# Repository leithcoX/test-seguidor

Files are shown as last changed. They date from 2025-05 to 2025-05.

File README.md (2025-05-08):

# Robot Seguidor de Línea

Test de seguidor de línea para competiciones.
Nombre pendiente.

## Estructura del proyecto
Boceto de la estructura del proyecto

```bash
.
├── placa_sensor
│   ├── kicad_sch
│   └── kicad_pcb
├── placa_seguidor
│   ├── kicad_sch
│   └── kicad_pcb
├── modelo
│   └── seguidor.FCStd
├── include
│   ├── file1.h
│   └── file2.h
├── src
│   ├── file1.ino
│   └── file2.ino
├── res
│   ├── datasheets.pdf
│   ├── images.png
│   └── referencias o links
└── README.md
```

## Requisitos
 - 20cm largo x 14cm de ancho x 10cm de alto
 - Area mínima de 23mm x 14mm. Visible. No pueden ser secciones de la batería.
 - No control remoto, o que solo de la orden de salida
 - Indicador luminoso (fijo o intermitente) que muestra cuando el robot inicia a correr.
 - Ruedas sin adherentes

## TODOs
 - ~~Rediseñar la placa de sensores (corregir errores) y mandar al lci~~
 - ~~Puente H~~
 - ~~Arduino Nano o ATmega328~~ y programarlo
 - ~~Comprar Placa Experimental~~
 - Elegir batería
 - Hacer un diagrama tal vez de como seguir el proyecto
 - ~~Hacér una bitácora~~ (subirla al repo?)
 - Agregar vista general del proyecto desde la página principal
 - ~~Agregar una lista de compras que puedan editar todos~~
 - Terminar de Soldar/limpiar modulo de sensores chequeando continuidad (Ciin lo hace el jueves)
 - Probar modulo se sensores con arduino (Armar código de prueba) 
 - 

## Artículos pendientes
 - 2 Capacitores 100nf (Puente H)
 - 10 x Diodos 1N4007  (Puente H)
 - 1 x Zócalo ZT16A (Zocalo 16 pines para puente H)

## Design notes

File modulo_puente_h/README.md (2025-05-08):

# Modulo Puente H

Este módulo se encarga de controlar los motores a partir de las entradas recibidas por sus pines.

Las pistas azules representan conexiones físicas cableadas por nosotros ya que el diseño no es posible en una placa simple faz.

![Front preview de la placa]() 


## TODOs
 - [ ] Revisar las medidas de la placa
 - [ ] Hacer los agujeros para las medidas del modelo 3D
 - [ ] El regulador de tensión debería ir en este módulo?
 - [ ] Revisar las conexiones
 - [ ] Replantearse el diseño del puente h, ¿Qué tensión tienen los motores?

#### Nota

Considerar que se podría diseñar todo en la parte posterior y soldar los componentes del lado que no tiene cobre.

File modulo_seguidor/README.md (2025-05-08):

# Modulo Seguidor

Este módulo se encarga de ejecutar las funciones propias de un seguidor de línea, procesar las lecturas del módulo sensor y dirigir los motores.

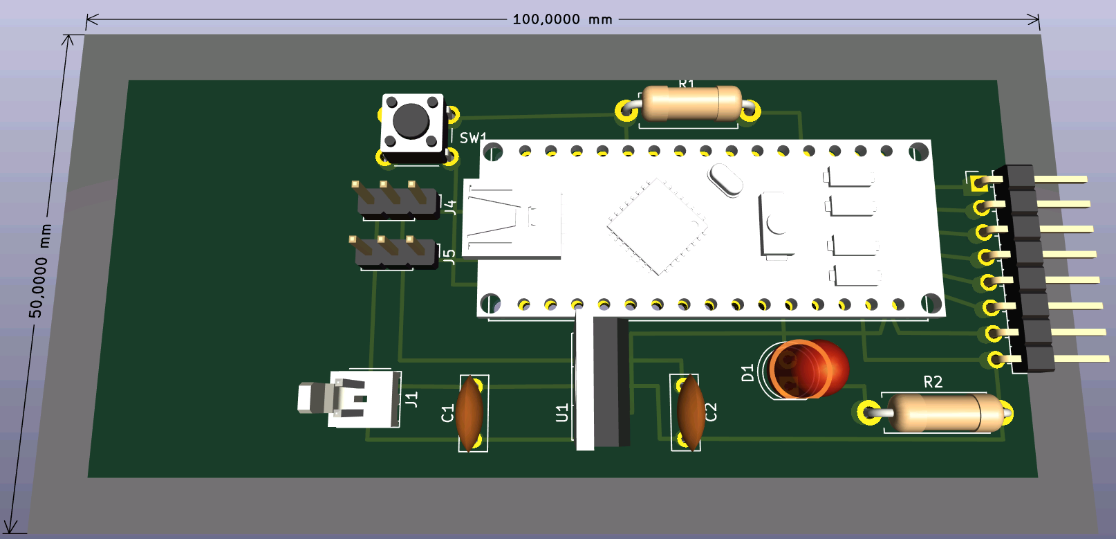
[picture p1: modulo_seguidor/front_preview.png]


Vista previa de la placa desde arriba

## Referencia

Para el diseño en kicad se realizó una configuración para editar la placa como si se editara una placa perforada.

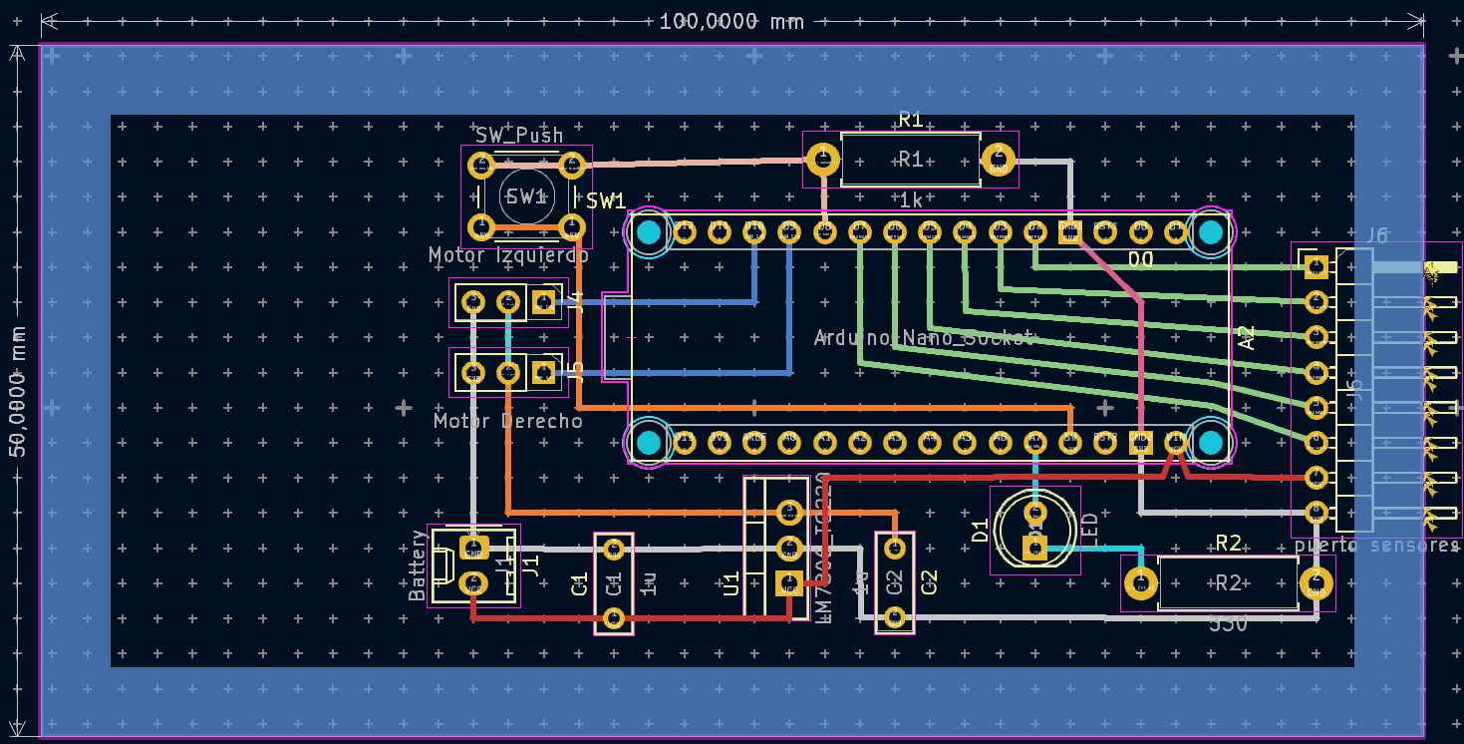
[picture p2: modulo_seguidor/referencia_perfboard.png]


Las marcas de cruces representan los agujeros de la placa perforada.
Las zonas sombreadas en los bordes tienen 5mm de ancho y representan la parte que no tiene agujeros en la placa perforada.
Si no se puede acomodar el componente se presiona CTRL mientras se arrastra para hacer un ajuste fino.

Más información al respecto en [foro de arduino](https://forum.arduino.cc/t/perfboard-circuit-design-with-kicad/1283999)

## TODOs
 - ~~Revisar las medidas de la placa (tomar en cuenta los bordes de la placa que no tienen agujeros)~~
 - Revisar los footprints de las resistencias y de los capacitores
 - ~~Acomodar los componentes y hacer las conexiones~~
 - Exportar a un modelo 3D (opcional)

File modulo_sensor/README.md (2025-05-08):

# Modulo de sensores

Este módulo se encarga de la lectura de la línea.

[comment]: Hacer_alguna_descripción_más

Vista previa de la PCB desde arriba



Vista previa de la PCB desde abajo



## TODOs
En orden de prioridad
- ~~Automatizar exportar los archivos de fabricación~~
- Hacer las pistas más grandes si es posible
- El script debe exportar a PDF ambos lados en la misma hoja conservando las dimensiones para imprimir el circuito.
- ~~Exportar a otros formatos (SVG, STEP, etc)~~
- Agregar alguna compatibilidad para Windows(?
- Agregar algun check para el momento de subir a Github
- Tal vez agregar algunas opciones para controlar el script(?
- Cambiar las rutas relativas con alguna variable de entorno(?

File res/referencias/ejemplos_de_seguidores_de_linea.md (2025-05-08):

## Links sobre distintos seguidores de linea 

https://youtu.be/CcIQNCyfTVk

https://tecnopatafisica.com/tecno3eso/teoria/robotica/105-arduino-robot-siguelineas

https://www.taloselectronics.com/blogs/tutoriales/robot-seguidor-de-linea-para-arduino-codigo

Referencia de internet


Un seguidor de línea del LABI
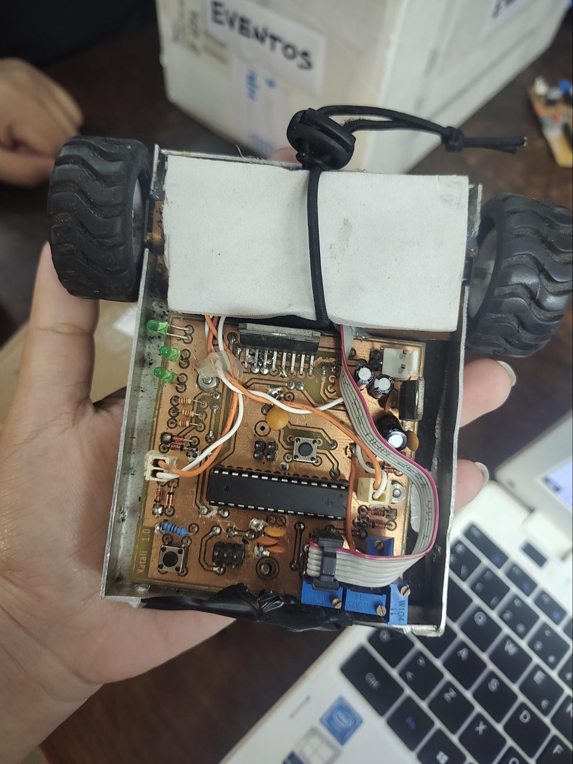
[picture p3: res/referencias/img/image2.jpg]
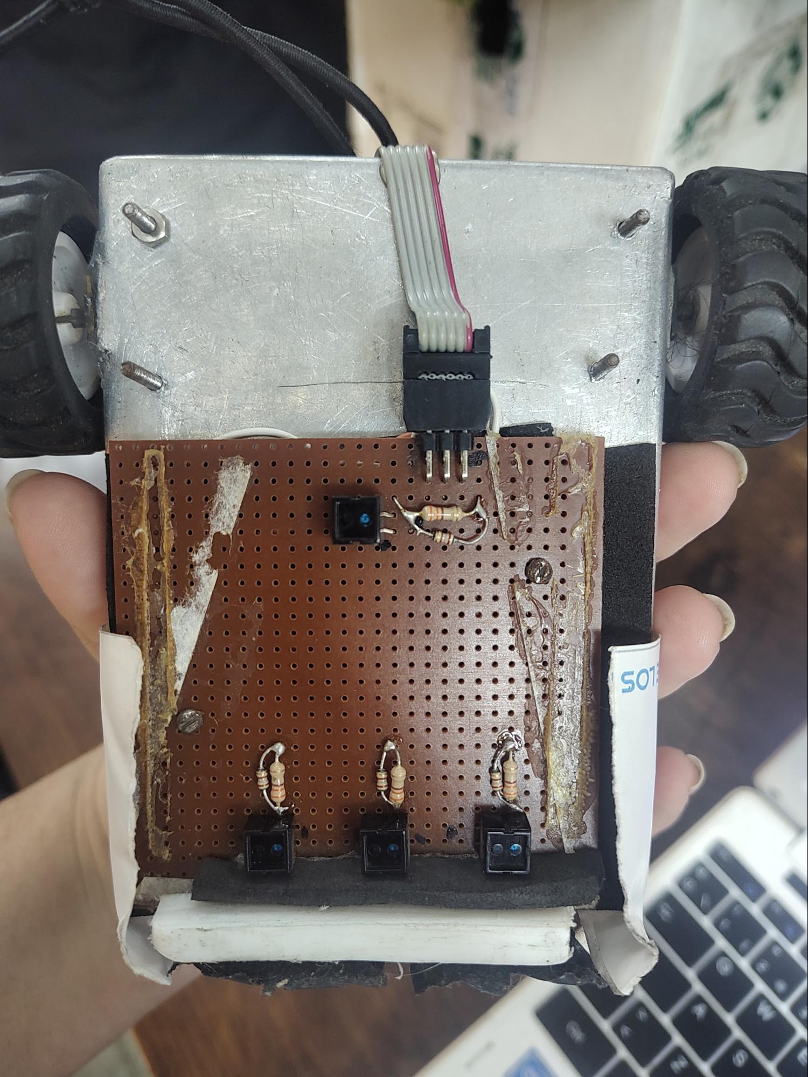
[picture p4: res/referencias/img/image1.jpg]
 

Otro más
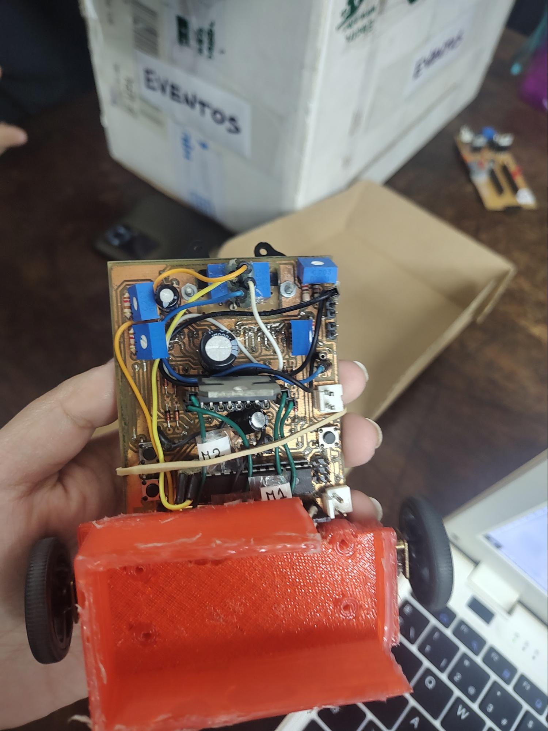
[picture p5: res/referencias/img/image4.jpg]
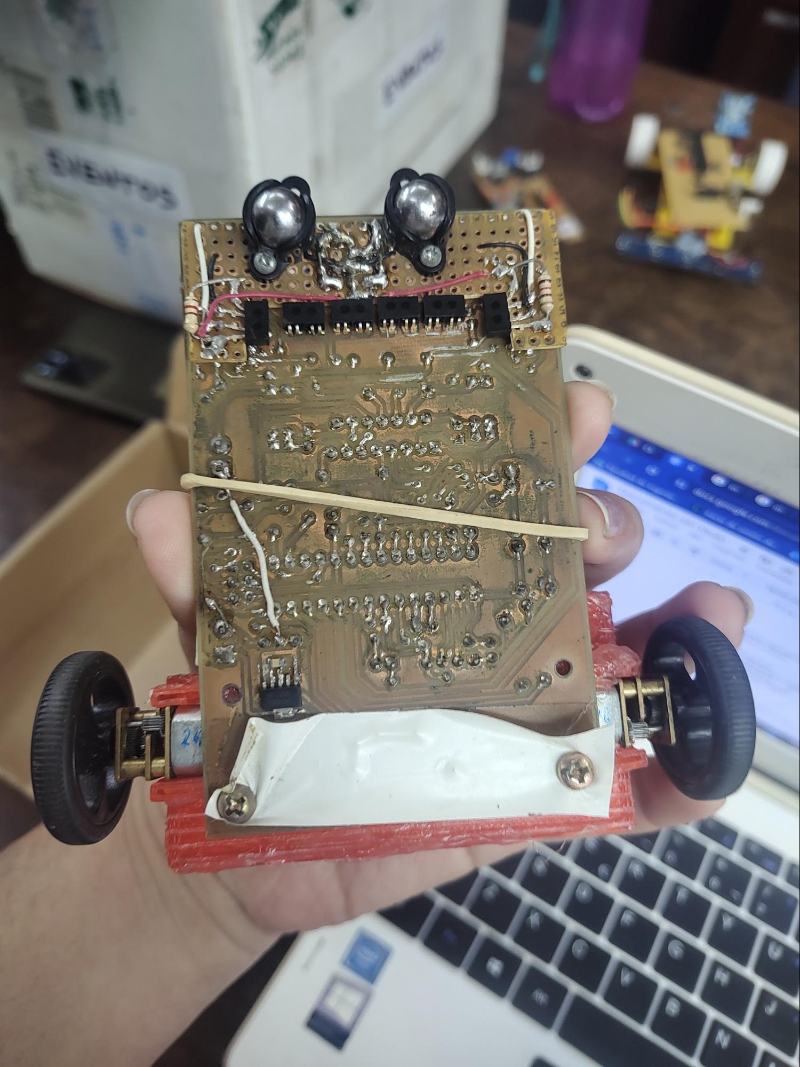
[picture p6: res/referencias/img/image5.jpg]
 

## Código

https://www.youtube.com/watch?v=w3bE3ygJMx8

## Puente H

Cómo usar un driver L298N

https://youtu.be/c0L4gNKwjRw?si=vZ1mv0ccFuuH0b-6

Esquemático de un driver genérico con L298N

https://newscrewdriver.com/2021/01/28/circuit-schematic-of-generic-l298n-driver-board/


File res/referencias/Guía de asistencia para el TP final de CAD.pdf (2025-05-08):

V2(2°Q 2020) | Guía de asistencia para el trabajo práctico final | ICAD 86.70

Autor: Zarauz Ignacio

## Guía de asistencia para el trabajo práctico final

Guía de asistencia para el trabajo práctico final

Introducción al diseño asistido por computadora (86.70) | 2

# Apartado técnico

Antes de continuar con la parte tangible del trabajo práctico asegúrese que su layout del PCB esté en condiciones. Verifique:

- Pistas: ancho indicado.
- Pads: tamaño apropiado (mínimo del área por defecto).
- Agujero de los pads: tamaño de sus brocas (recomendado, no esencial).

El ancho de sus pistas es de 20 mils (0,5 mm aproximadamente) ¿Qué importancia tiene esto? La importancia de esto será especificada más adelante.

La lista de precauciones para el PCB a continuación se debería detallar para explicar porque se deben aplicar, pero no se encuentra al alcance de las herramientas de física 2 (la cual, según el plan de estudios, se debe cursar en paralelo o antes de esta materia):

- Conectar el relleno de cobre a masa.
- Evitar pliegues de pistas en ángulos rectos.

El ancho de las pistas queda acotado por factores económicos, físicos y prácticos. Si hacemos pistas muy anchas estas ocuparán mayor superficie, el circuito aumentará de tamaño y necesitaremos placas muy grandes. Si fueran pistas fueran angostas existen al menos 3 problemas: el primero es que si decidimos hacer la placa con algún método poco profesional (como el del planchado) es probable que no queden fijadas las pistas sobre el cobre, en caso de que mejoremos el trazado de las pistas sobre el cobre todavía sigue siendo un riesgo el hecho de que el ácido puede comérselas. Si logramos resolver estos asuntos con técnicas profesionales aún queda un inconveniente físico que no podemos saltear.

# Realización del PCB

## ¿Qué ancho deben tener las pistas?

Seguro se habrá preguntado si existe algún motivo, además de la consigna, para elegir un ancho de 20 mils. A continuación, se trata de explicar con qué criterio puede escoger el ancho.

Si ya ha cursado física 2 sabrá que densidad de corriente es corriente sobre área. Básicamente, corriente es, un flujo de electrones en un área. Ahora ¿Cuál es nuestra área? Nuestra área es la sección de cobre de la pista, esta área depende de la altura del cobre (de la cual se hablará en la parte de ácido clorhídrico) que viene de fábrica y el ancho, el cual se lo da el ancho de la pista.

Al disminuir el ancho es totalmente análogo a quitar carriles de una autopista. Si sacamos carriles a la autopista el transito se empieza entorpecer y los autos deben circular con más cuidado para no chocarse unos con otros. Si seguimos sacando carriles llegará un momento en que no podrán circular más los autos. Algo similar ocurre con los electrones de la pista. Físicamente hablando, al disminuir el área la pista deja de funcionar como un conductor y empieza a ser una resistencia. Esto explica porque no podemos hacer tan fina la pista de cobre. En caso de haber corriente suficiente para hacer funcionar el dispositivo conectado a esa pista se podrían hacer trazados muy finos hasta el límite mínimo necesario para el dispositivo.

Para seguir manteniendo la corriente la tensión debe aumentar y esto provoca que la pista se caliente para disipar la energía. Como método alternativo a aumentar las pistas de ancho, en circuitos que ya tienen pistas muy anchas, algunos recurren a bañar la pista de cobre con estaño que, a pesar de no tener la misma conductividad que el cobre, es un buen conductor.

A continuación, y a lo largo de la parte técnica del documento, se encontrará con una selección de videos formativos útiles para la realización del trabajo. También se encontrarán videos optativos, de características informativas, que cumplen la función de complementar lo aprendido en la materia con usos que quedan fuera de los límites de la materia, pero que están vinculados a ella.

## Método de planchado

Este es, en caso de que no lo manden al LCI u otro servicio que se dedique a
realizar | PCB, | el | método | más
recomendado y barato. Parte del trabajo práctico es que pase por esta experiencia. Que sea barato no implica que sea de mala calidad, simplemente que las características del circuito, función y cantidad no son las indicadas para mandar a fabricar o realizar con el método de serigrafía.

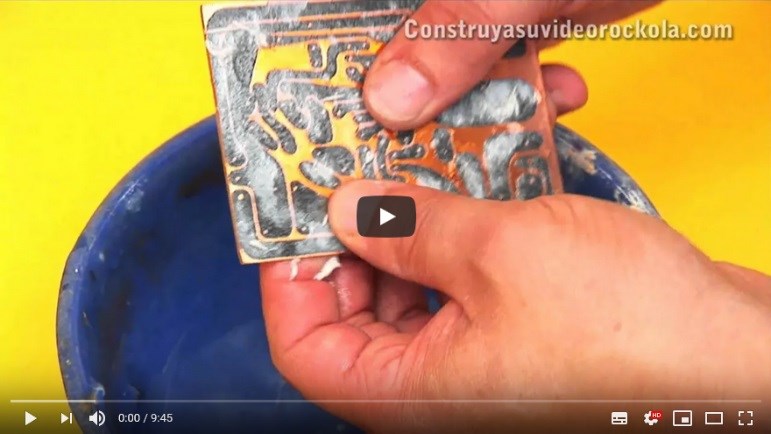
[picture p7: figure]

En cuanto a las técnicas las variantes que se pueden señalar es que en lugar de usar Thinner para remover el tóner se puede usar esponja de acero (virulana o la marca que sea), la misma que usa para limpiar el cobre antes de planchar. Es muy importante que la limpie. Asegúrese de usar la virulana que literalmente tiene densidad de esponja, visualmente esta está hecha de pequeñas fibras metálicas suaves que al usarla desprende fibras de la esponja. Se usa para limpiar metales blandos (bronce, cobre) ya que corren menos riesgo de ser rayados y le retiran los óxidos depositados.

Otro consejo, es que, al planchar, no solo limpie la placa, asegúrese que su impresión tenga el tamaño y espejado adecuado (cuando quede la tinta adherida al cobre debe verlo como quedará finalmente) y cuando vaya a colocar la hoja sobre el cobre preste mucha atención respecto a los bordes y la alineación. Si lo hace con cuidado, puede recortar primero la placa de cobre al tamaño de su circuito, o con un milímetro de margen si hay pistas pegadas al borde (recomendamos comprar una placa de 5x10 para tener al menos 2 intentos), para que el ácido tarde menos tiempo en retirar el cobre.

En cuanto a la alineación, al planchar, muchas veces no sale como uno espera. Recuerde hacerle unos márgenes, respecto a la impresión, al papel para que cumplan función de solapas que se plieguen al final de la placa la rodeen para pegarla con cinta. En caso de tener seguridad, y experiencia, podría poner una solapa y el resto mantenerlo con cinta a lo largo del borde. Esto no se recomienda mucho, ya que la cinta entorpece la conducción adecuada del calor hacia la tinta. Por la dificultad mencionada, se recomienda crear un PDF con múltiples cantidades de la impresión del PCB. Esto se puede hacer en una hoja usando programas como Inkscape, que es gratuito. Cuando lo haga asegúrese de que el dibujo conserve su tamaño original ¡lo mismo cuando ya este impreso! (las impresoras a veces están configuradas de manera tal que las dimensiones de la imagen se distorsionan). Puede aprovechar para crear una máscara de componentes casera (asegúrese de que el espejado sea el adecuado) imprimiendo la capa F.Fab (sobre la misma hoja) y planchándolo sobre la otra cara de la placa. Esto último suele salir mal, afortunadamente no es necesario para el trabajo. Requiere de más tiempo de planchado que la parte de cobre. También puede coordinar con compañeros para poner más de un modelo de PCB en la misma hoja.

Consejos para planchar. Si nunca ha tocado una es buen momento para aprender. No necesita experiencia previa. Claramente hágalo en seco (sin líquidos). Recuerde que es sobre la parte de cobre con algún papel entre la hoja de transferencia y la plancha. El tiempo de planchado depende de la potencia de la plancha y el papel de transferencia. Con una plancha por encima de los 80°C con 5 minutos en el lado del cobre alcanza (para el F.Fab puede necesitar 10). Puede dejar durante algún momento la plancha encima de este, pero durante al menos 2 minutos deslice con presión sobre el PCB, especialmente en los bordes y trozos de cinta, los bordes son muy importantes. Para darle unos retoques finales puede planchar directamente sobre el papel transfer. Una vez planchado sumergir inmediatamente en agua.

Una vez metido en el agua empezara a ver el resultado. Con las yemas de los dedos podrá retirar el papel. Algunos papeles dejan restos sobre los lugares que deberían ser comidos por el ácido. Para disminuir el tiempo en el ácido se recomienda repasar con un punzón aquellos lugares con el cobre expuesto. En caso de que alguna pista se haya cortado en el procedimiento este o el planchado se puede rescatar repasando, en el lugar que debería estar cubierto, con tinta con un marcador negro de tinta indeleble. Por experiencia, el Sharpie indeleble anda muy bien.

Algunos de los materiales, como la plancha, son comunes en los hogares, otros, como el ácido, posiblemente tenga que comprarlos. El Labi cuenta con plancha y herramientas para realizar este proceso. Lo único que tendría que aportar es un envase de plástico para poner el ácido y el ácido. El Labi le puede facilitar un papel de revista e imprimirlo en la fotocopiadora de la facultad. En caso de imprimirlo en su casa tenga en cuenta que la impresora debe ser laser y que las librerías y fotocopiadoras no dejan que les metan hojas texturas extrañas a sus fotocopiadoras o impresoras.

Antes de proseguir con otros videos esta bueno aclararle algunas cuestiones sobre el percloruro férrico, más allá de los cuidados que deba tomar (evitar contacto con la piel, ropa y superficies metálicas, opcional usar guantes, espacio ventilado y regular conscientemente la temperatura), para que pueda operar con un poco de conocimiento encima.

Cantidad y tiempo dependen de:

- Superficie placa.
- Superficie a comer.
- Temperatura del ácido.
- Movimiento del ácido.
- Concentración del ácido.

El percloruro férrico puede ser vendido como polvo o diluido (las proporciones varían). Lo más probable es que lo consiga en liquido (diluido), lo cual es parcialmente más seguro dado que evita aspirar partículas de polvo. A continuación, se hablará de las características que hay que contemplar acerca de este. El tiempo para una placa de estas dimensiones totalmente cubierta suele ser de más de 15 minutos.

Si la placa fuera más grande, seguro, sería más la cantidad de cobre a retirar. El mismo problema sucede si no está hecho el copper pour, ya que se retiran superficies de cobre que no influyen en este trabajo y el tiempo del proceso será mayor. Una alternativa al copper pour, que en este caso no se puede, es agrandar algunas pistas.

La eficiencia del ácido aumenta con temperaturas altas. En caso de tenerlo en polvo, caliente agua donde lo diluirá (los vapores son nocivos para la salud). En caso de tenerlo líquido ponga el recipiente del ácido (puede ser un frasco de mermelada) en baño maría (una olla, por ejemplo). También puede hacerlo sin calentar, recomendable solo si la solución es nueva.

Una solución nueva es una solución que no ha sido utilizada antes. Una vez usado, el ácido, sigue siendo útil para el mismo propósito. Puede meterlo en un recipiente distinto o mezclarlo con el resto de la solución nueva (perderá eficiencia). Esto es ocasionado porque en la reacción se pierden reactivos y quedan productos en la nueva solución. Esto indica que la concentración del ácido no viene dada solo por las partes que se pongan de ácido (en polvo) con agua, sino que también influye en cuantas veces se usó antes.

Para esto hay que tener en cuenta:

- Reacción química:
- FeCl3(ac) + Cu(s) → FeCl2 + CuCl (ecuación de interés)
- Densidad cobre: 8.96 g/cm³
- Densidad percloruro férrico: 2.9 g/cm³
- Densidad agua: 1 g/cm³
- Masa molar cobre: 63,546 g/mol
- Masa molar percloruro ferrico: 162.2 g/mol
- Grosor placa (posibles valores con cobre incluido):
- 0,4 mm
- 0,8 mm
- 1,2 mm
- 1,6 mm
- 2 mm
- 3 mm
- Grosor cobre (1 onza cobre /pie² ):
- ½ onza = 17,5 micrones
- 1 onza = 35 micrones
- 2 onzas = 70 micrones
- 3 onzas = 105 micrones

Pie= 4 pulgadas= 4*2,56 cm

Micrones = 1/1000 mm de espesor

Onzas = 28,7 g

Supongamos un ejemplo. Se quiere retirar todo el cobre de una placa de cobre de 3 onzas, con un tamaño de 40 por 40 milímetros. Esto daría un volumen de cobre de 0,168 cm³
. La masa de este
sería de 1,505 g. La cantidad moles sería de 0,023688. Como la reacción indica que necesitamos 1 mol de ácido por 1 mol de cobre se necesitaría la misma cantidad de moles de percloruro de hierro (III) que de cobre. Sería una masa de 3,842 g y un volumen de 1,3249 cm³ de este último.

Según esos datos sería muy sencillo y rápido el proceso. Pero hay varios factores de la cinética química que no colocamos en los datos. Para que se dé una idea, se necesitan 60 cm³ de solución, al 40%, de percloruro férrico, de primer uso, a 45°C durante 10 minutos, por lo menos, para poder realizar este trabajo.

A medida que ocurre la reacción se depositan productos sobre la placa evitando que los reactivos entren en contacto. Para evitar esto se incorpora un proceso más para acelerar la reacción. El hecho de agitar levemente el ácido ocasiona que en todo momento esté la posibilidad de que entren en contacto los reactivos y sean arrastrados los productos. Cabe aclarar que también quedan otras basuras como restos del papel transfer. Agite de manera prolija: sirve tanto revolver, que puede no ser tan eficiente, como zarandear moderadamente el envase de ácido.

En caso de tener todos los factores a favor es probable que pueda tener su placa fuera del ácido en 10 minutos. El sobrante del ácido recomendamos guardarlo (tirarlo a las cañerías podría ocasionar daños). Limpiar el envase con un papel y tirarlo a la basura. El ácido diluido no es lo suficientemente fuerte para quemar instantáneamente, pero le recomendamos pasarse un poco de papel y lavarse las manos en caso de tocarlo. Existen otros ácidos más fuertes que suelen servir, como el ácido nítrico, pero recomendamos usar el mencionado en la explicación.

Si bien pierde calidad el ácido usado, existen métodos para recuperarlo. En internet hay métodos que explican cómo. Para ahondar más en este tema y obtener la verdadera formulación química de esta reacción sugerimos que le pregunte a un profesor de química, ya que estos temas se ven abordados en dicha materia.

Es muy importante la limpieza de la
placa, ya que, aunque no lo veamos
existen suciedades, como el óxido, que nos podrían dificultar el trabajo. Una superficie con óxido dificulta la soldadura y evita el contacto adecuado con las puntas del
multímetro | para | medir
continuidades.

Se expone como alternativa mirar

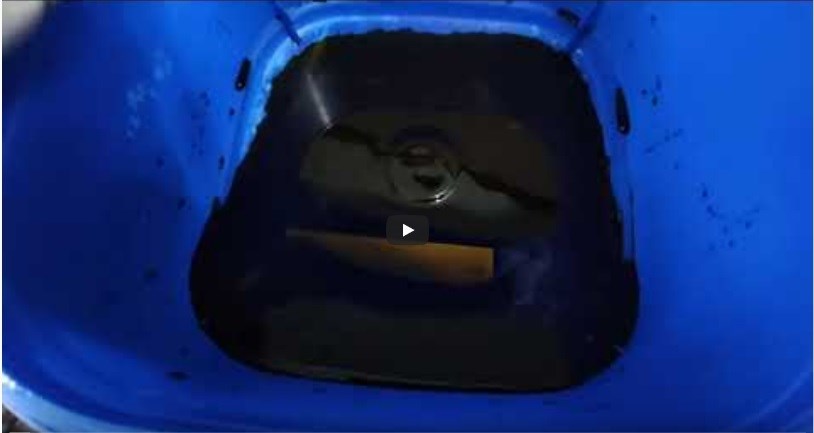
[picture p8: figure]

este video hecho por uno de los colaboradores de la cátedra para realizar el método de planchado.

Un detalle más: la velocidad y prolijidad de la reacción del ácido esta fuertemente vinculada con el tipo de papel que se use.

## Materiales

- Placa de cobre simple faz.
- Papel de revista, glossy, transfer o satinado.
- Impresora láser (una impresión).
- Plancha (de ropa).
- Percloruro férrico (u otro ácido apto).
- Envase apto para ácido (vidrio si se quiere calentar o plástico).
- Envase para colocar ácido sobrante.
- Agua en un envase.
- Cinta adhesiva (puede o no ser kapton).
- Guantes o pinza no metálica (para manipular la placa en el ácido).
- Lana de acero.
- Marcador indeleble.
- Herramienta punzante (retirar papel innecesario y sobrantes de cobre o agrandar agujeros).
- Herramienta de corte (cutter, formon, ciertas guillotinas, minitorno, caladora, etc).
- Herramientas de perforación (minitorno, taladro de banco o cualquier variedad de taladro manual o automático que pueda usar brocas de 0,5 mm a 1,5 mm).
- Flux (opcional)
- Alcohol isopropílico (opcional).
- Aguarrás/quitaesmalte/Thinner (opcional).

## Método de serigrafía

Para los usuarios comunes aparte del método de planchado existe el de serigrafía. Como se ve en el video, no es recomendable por su alto costo y demanda de tiempo. El método profesional de hacer PCB, de hecho, se parece demasiado a esto. Podrán observar el método profesional de hacerlo multi capa (si, no solo se hace con capas de ambos lados, sino que además se pueden incorporar capas

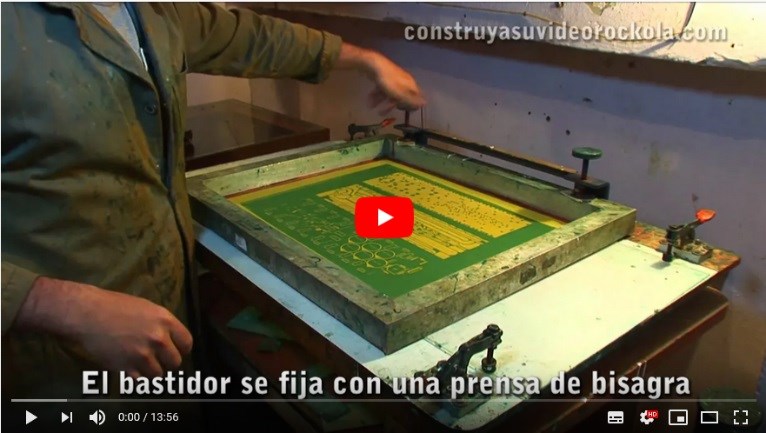
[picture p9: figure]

internas) en los videos que siguen. Este método es una simplificación para 1 o 2 capas.

## Materiales

- Placa de cobre simple faz.
- Percloruro férrico (u otro ácido apto).
- Envase apto para ácido (vidrio o plástico).
- Agua en un envase.
- Cinta (puede o no ser kapton).
- Guantes o pinza no metálica (para manipular la placa en el ácido).
- Envase para colocar ácido sobrante.
- Lana de acero (opcional).
- Herramienta punzante (retirar papel innecesario y sobrantes de cobre o agrandar agujeros).
- Alcohol isopropílico (opcional).
- Aguarrás/quitaesmalte/Thinner (opcional).
- Herramienta de corte (cutter, formon, ciertas guillotinas, minitorno, caladora, etc).
- Herramientas de perforación (minitorno, taladro de banco o cualquier variedad de taladro manual o automático que pueda usar brocas de 0,5 mm a 1,5 mm).
- Shablon o bastidor de 120 hilos.
- Emulsión y revelador.

- Cámara de luz UV (tiene que entrar el bastidor)
- Acetato y una impresión adecuada para este.
- Pintura UV para PCB (para el cobre, antisoldante y serigrafía)
- Espátula.
- Soda caustica (diluida).

Existen otros métodos de tratamiento UV, como la lámina sensible a UV. En el LCI (Laboratorio de Circuitos Impresos) (http://lci.labi.fi.uba.ar/) utilizan ese método. Imprimen sobre una lámina transparente con una impresora especial un negativo del circuito (en lugar de imprimir el camino de cobre imprime lo contrario, cabe destacar que la impresión debe ser
sumamente opaca y sin poros). Dicho
negativo lo ponen sobre una lámina UV

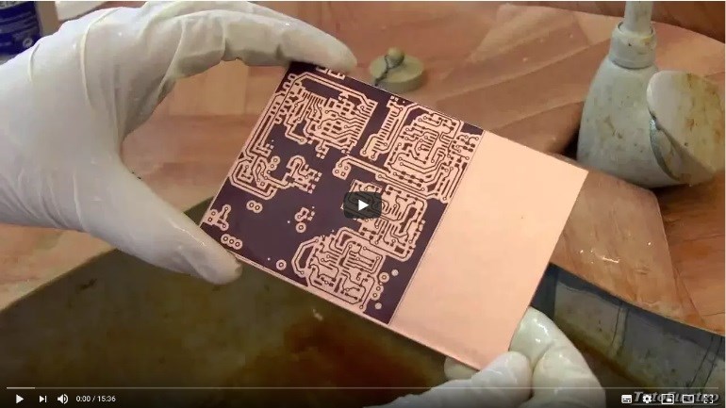
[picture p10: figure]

y dicha lámina sobre la placa de cobre. Se expone esa composición a una cámara con luz UV. Como la luz UV no atraviesa el negativo, porque está la tinta, solo afecta los sectores transparentes, haciendo que se adhiera la lámina en los caminos de cobre que deseamos conservar. Así, la lámina, cumple el mismo rol que el tóner en el caso del planchado. El resto del proceso es similar, pero usan otro ácido.

## Materiales

- Placa de cobre simple faz.
- Lamina fotosensible.
- Liquido revelador.
- Cámara de luz UV
- Percloruro férrico (u otro ácido apto).
- Envase apto para ácido (vidrio o plástico).
- Agua en un envase.
- Cinta adhesiva (puede o no ser kapton).
- Guantes o pinza no metálica (para manipular la placa en el ácido).

- Envase para colocar ácido sobrante.
- Lana de acero.
- Marcador indeleble.
- Herramienta punzante (retirar papel innecesario y sobrantes de cobre o agrandar agujeros).
- Herramienta de corte (cutter, formón, ciertas guillotinas, minitorno, caladora, etc).
- Herramientas de perforación (minitorno, taladro de banco o cualquier variedad de taladro manual o automático que pueda usar brocas de 0,5 mm a 1,5 mm).
- Brocas de 0,5 mm a 1,5 mm de acuerdo a necesidad.
- Alcohol isopropílico (opcional).
- Aguarrás/quitaesmalte/Thinner (opcional).

## Fabricación de una cámara UV casera [opcional]

A comparación de la cámara UV planteada en el video de serigrafía esta parece mucho más económica y de tamaño reducido ¿valdrá la pena? Eso se puede observar en el siguiente video.

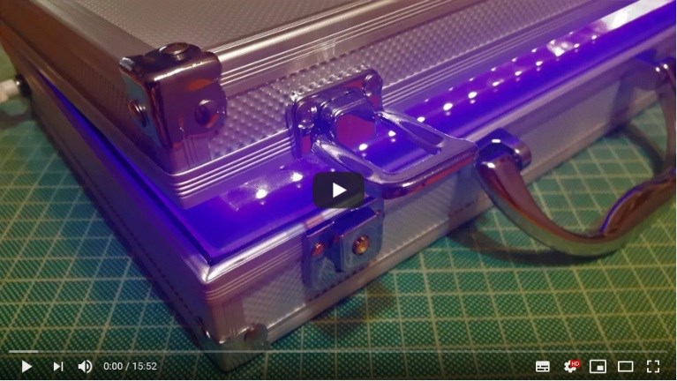
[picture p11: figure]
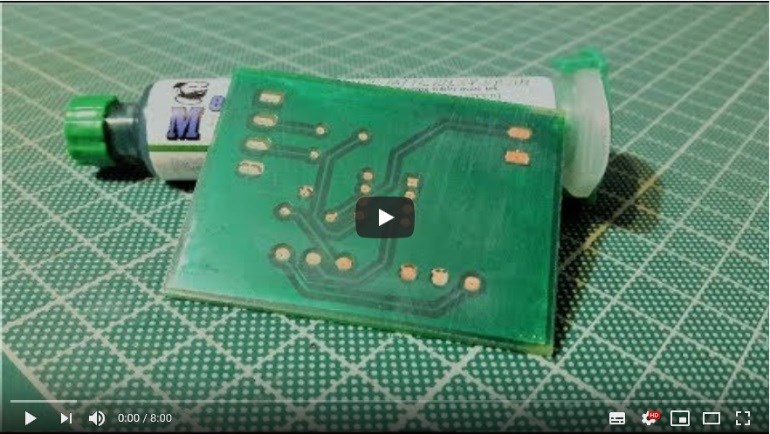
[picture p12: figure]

Como se ve en el video, la cámara
funciona. | También | sirve | como
experiencia para saber que este método es mucho más complicado que el de planchado, ya que hay que prestar atención a que no se mueva el negativo. De cualquier manera, esta máscara no se puede realizar con un método más sencillo que este.

## Perforación del PCB

Una vez que la placa parece estar lista límpiela (puede usar la esponja de acero ya mencionada y alcohol, isopropílico en lo posible), revise continuidades, que no haya cortocircuitos ni pistas cortadas, corte los sobrantes y lije los bordes. Tenga cuidado con el polvo y siempre deje limpio el lugar de trabajo. El próximo paso será perforar la placa. Deberá abastecerse de brocas de acuerdo al tamaño de los pines de sus

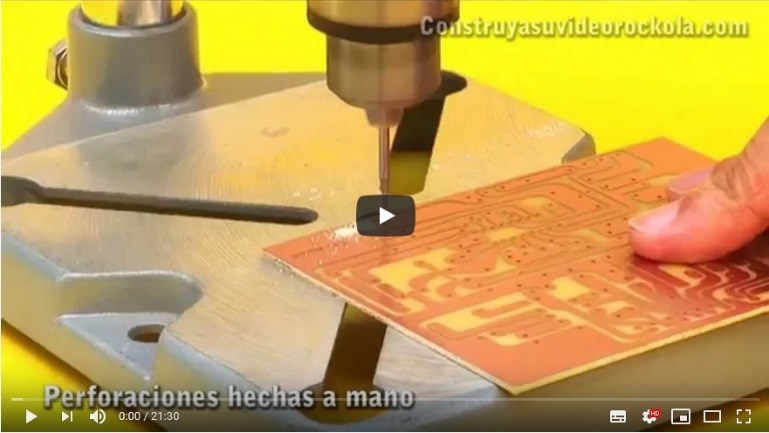
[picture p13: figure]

componentes. Revise la sección de “abastecimiento de materiales” para obtener información de donde comprar dichos elementos.
En caso de no contar con minitorno, Dremel o torno de banco, podrá usar el del Labi. Usted deberá llevar sus propias brocas. Recomendamos comprar un par de 3 tamaños (0,7 a 1,5) mm entre compañeros. Las de 0,7 mm se rompen muy fácil.

## Método de CNC

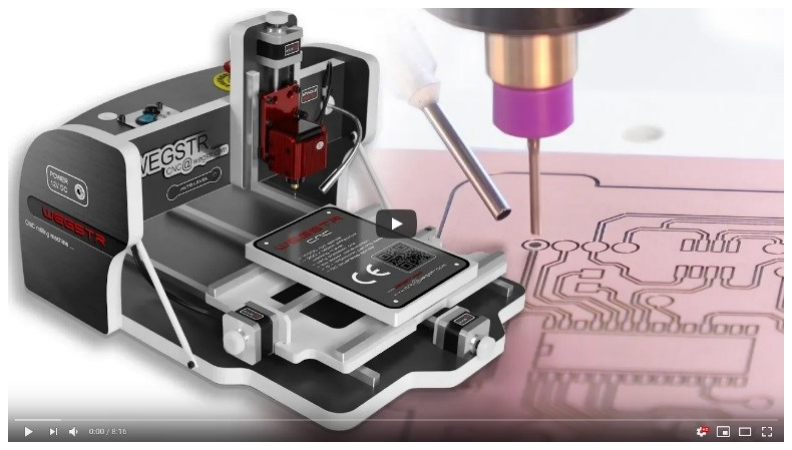
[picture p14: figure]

Un | método | muy | rústico | y
contemporáneo es usar una fresadora automática para devastar la superficie de cobre con una fresa y evitar el uso del ácido y sus riesgos.
Dicha fresadora cambia de broca y se usa el mismo programa con otro recorrido para hacer el corte y los agujeros tal y como se vio en la perforación de PCB con CNC.

## Materiales

- Placa de cobre simple faz para PCB.
- Brocas y puntas devastadoras adecuada para retirar hasta 0,1 mm de cobre del PCB.
- Fresadora automática apta para devastar la superficie de cobre.

## Fabricación de PCB multicapa

Una vez entendidos los anteriores videos seguro está tiene las capacidades para proseguir con el siguiente nivel. En esta sección se mostrará a lo largo de 4 videos la confección de PCB multicapa. El primer video nos ofrece una síntesis bastante clara, en español, de cómo es el proceso. La capacidad a nivel doméstico permite hacer PCB de 1 o 2 capas, sin embargo, en PCB de alta complejidad son muy común las capas

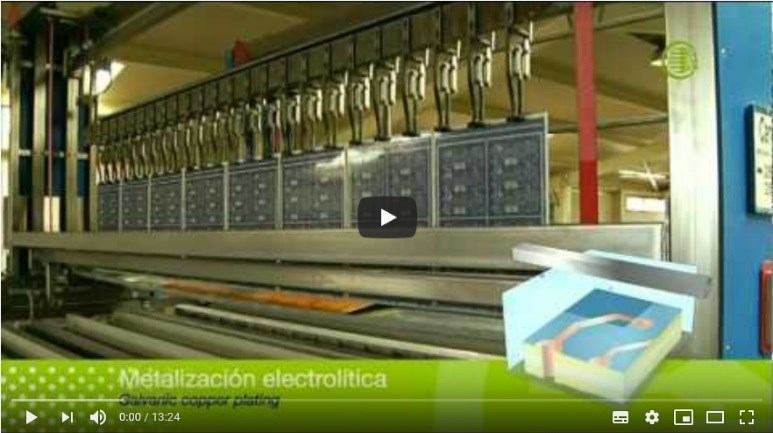
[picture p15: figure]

internas en dispositivos avanzados.
El segundo video muestra un recorrido mucho más completo y complejo. Cabe destacar que la dificultad del video no está dada solo por la longitud del mismo y el inglés técnico y preciso que se maneja (en español muchas de esas
palabras se usan sin traducir), sino que
además incorpora procesos e imágenes
que no resultan familiares.
Estos videos pretenden informar para satisfacer su curiosidad con el fin de saber cómo es el proceso para armar las pistas cuando no están a un lado o a otro de la placa, sino que están al medio. No
pretenda | que | sean | de | carácter
formativo, aunque con todas las

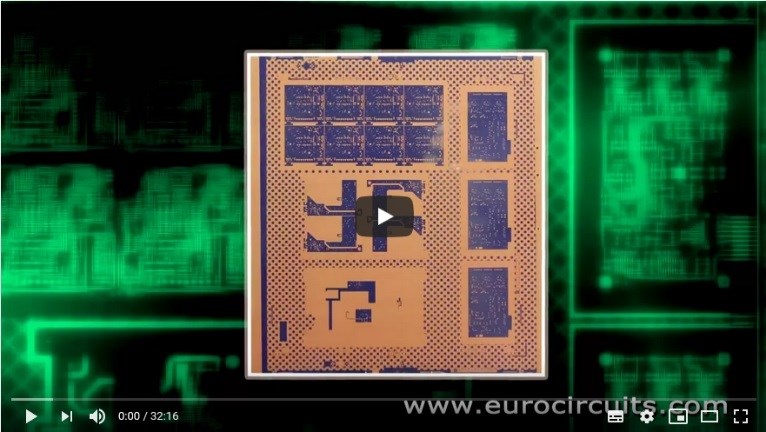
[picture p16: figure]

imágenes, explicaciones y videos, se podrá dar una muy buena idea de cómo funciona el sistema y las fábricas de estos.
En el tercer video, notará que es el mismo proceso, en una fábrica distinta. Sin embargo, el uso de distintas instalaciones implica otro tipo de mano de obra, maquinas automatizadas, métodos e incluso otras condiciones necesarias para el mantenimiento y la producción eficaz. Note, por ejemplo, que las cámaras donde se trabaja con film foto sensible utilizan iluminación amarilla. Esto es algo que tienen en común y es un detalle esencial. Se pueden considerar medidas flexibles contrastándolas con las fábricas que realizan circuitos integrados. Estas utilizan técnicas similares (a nivel microscópico) pero el

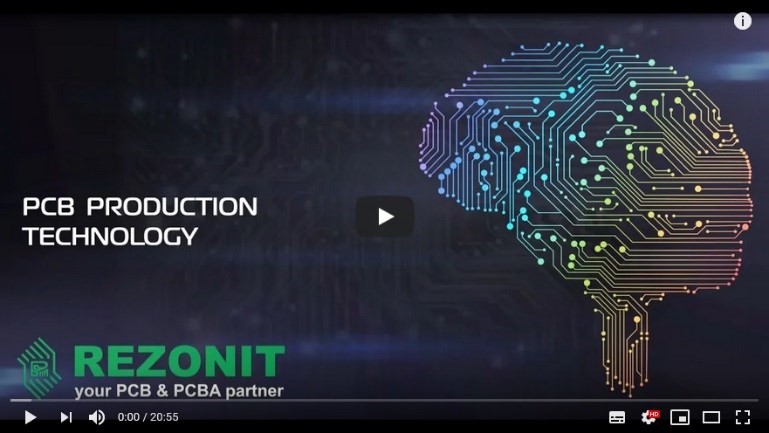
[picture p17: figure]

acondicionamiento del lugar es más minucioso: no solo necesitan tener cuidado con la luz, el aire del ambiente debe tener menos de 100 partículas cada 30 litros de aire. Esto se logra con sistemas de acondicionamiento de aire muy complejos, cámaras especiales para pasar a la sala de producción y operarios vestidos con un mameluco que los cubre totalmente (cabeza, cara y manos incluidas).

Este último video vuelve a mostrarnos una fábrica de Euro. A diferencia del anterior, este muestra un trabajo con más personas (note que las otras instalaciones tenían el traslado de placas a cargo de máquinas) y muestran el empaquetamiento del producto.
En el trabajo profesional no deberá realizar la placa por su cuenta. Esta
materia es una introducción al diseño
asistido | por | computadora, | una

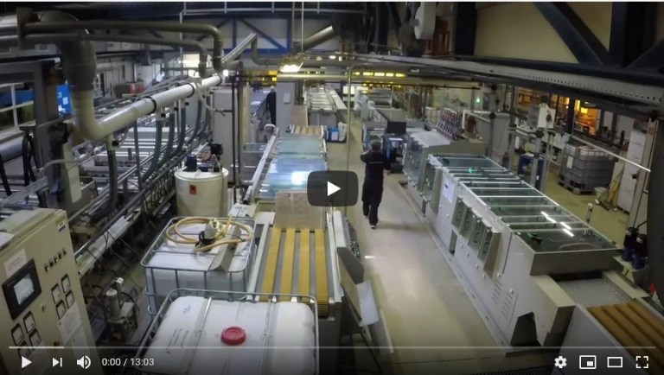
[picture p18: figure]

herramienta para que pueda apoyarse en los conceptos básicos de armado de PCB mediante softwares EDA más potentes que el KiCAD (claramente son pagos y pueden llegar a valer mucho dinero). Entenderá que lo trabajado en la materia es la introducción al paso previo a la realización de los PCB. Es muy común la utilización de páginas de internet para la realización de circuitos en volúmenes altos a un muy bajo precio. Estás fábricas abiertas al público común mediante internet suelen ser de origen chino.

## Soldado y desoldado de componentes

Una | vez | perforado | el | circuito
(terminado el PCB) deberá ensamblar los componentes. Como se ha trabajado
en | la | materia, | deberá | usar
componentes THT, sin embargo, estos consejos de soldadura le deberían ayudar. Este apunte del Labi (http://labi.fi.uba.ar/sites/default/files/cursos/soldadura/curso_soldadura.pdf) le enseñará a soldar y estos videosle mostrará cómo se hace. Es muy posible que tenga problemas para soldar al principio. Es cuestión de práctica y no hay manera de

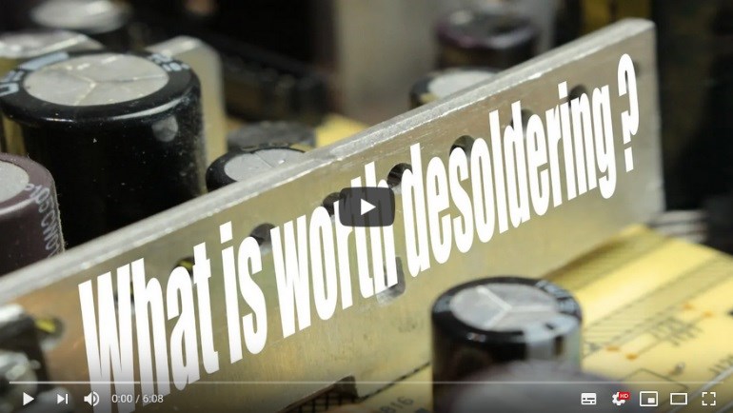
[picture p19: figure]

explicar cómo se hace para que lo haga perfecto, pero puede evitar errores.
El primer video habla, la mayoría del tiempo, sobre que vale la pena desoldar de una placa electrónica, aunque da muy buenos consejos, como tener un sistema de extracción de humo y vapores. Agregaría el uso de
pinzas y palancas para retirar o poner
componentes y ayudarse con flux.
El segundo video aporta información más básica y primordial para soldar. Evitar estos errores le ahorrara algunas frustraciones, aunque hay errores, como levantar una pista, que a veces vienen dados por el diseño de la placa. Lo único que no queda cubierto con este material es la soldadura con SMD.

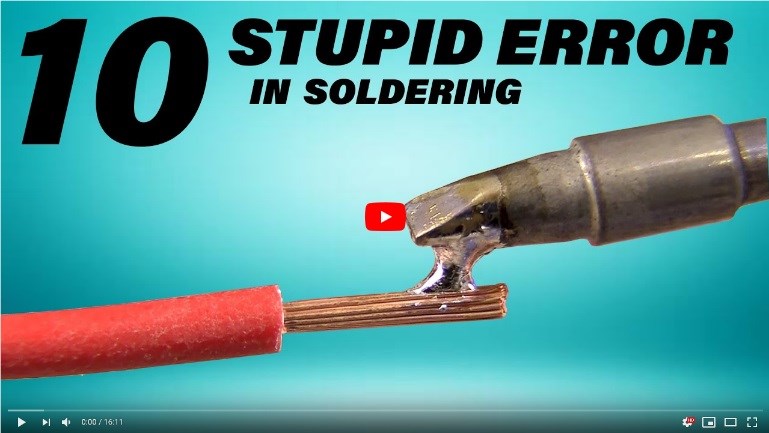
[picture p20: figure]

## Montaje de componentes en placas (Argentina) [opcional]

Como se ve en este video, en Argentina también existe una industria electrónica,
dedicada | al ensamblaje | de PCB
mostrados en videos anteriores, con máquinas automatizadas.

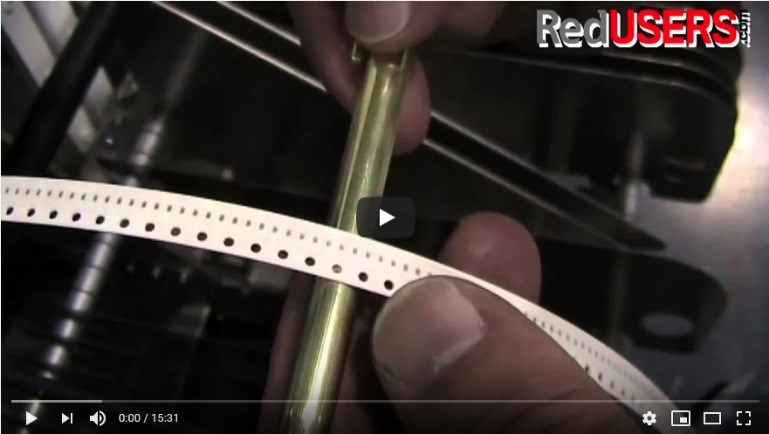
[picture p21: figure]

## Montaje de componentes placas (Asia) [opcional]

Acá se puede ver otra ensambladora, en Asia, más concentrada de espacio, con otros volúmenes de producción y otras rigurosidades en el ambiente.

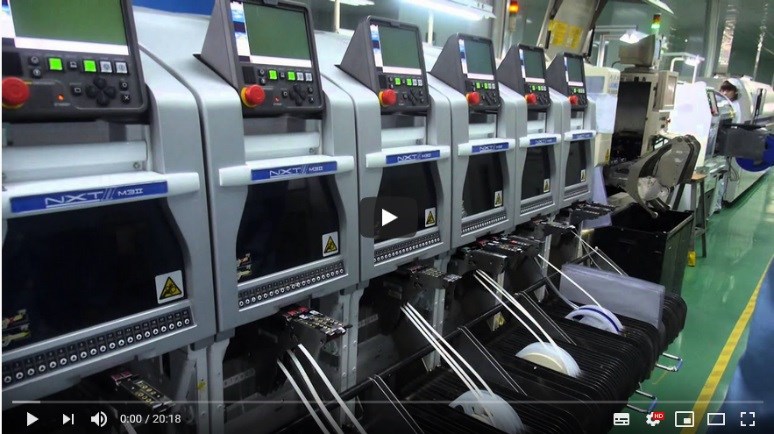
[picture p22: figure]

## ¿Qué hay dentro de un circuito integrado? [opcional]

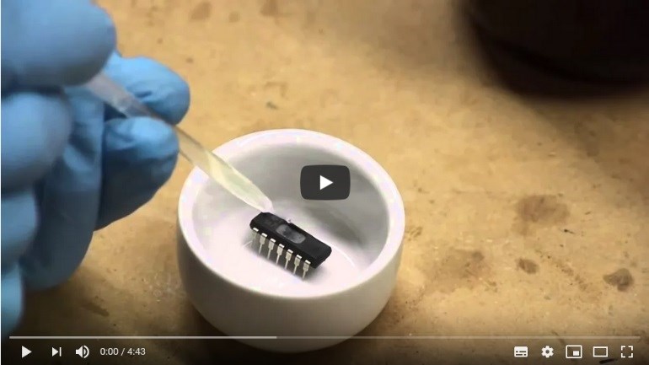
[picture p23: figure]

Dentro de un integrado hay un circuito con componentes microscópicos hechos de dispositivos semiconductores. El esquemático de un integrado es muy similar al de un circuito macroscópico. Durante la cursada ha tenido la oportunidad de ver el esquemático del 555.

# Abastecimiento de materiales

Puede comprar sus materiales y componentes en cualquier lugar, pero estos están enlistados debido a su cercanía al centro de CABA y la sede de Paseo Colón.

Brocas: Casa Wasser (https://www.google.com/maps/place/CASA+WASSER/@-34.606679,-58.3834462,15z/data=!4m5!3m4!1s0x0:0x85e383baee8771a3!8m2!3d-34.606679!4d-58.3834462)

Componentes electrónicos: Microelectrónica (http://www.microelectronicash.com/ofertas.php) y SYC (http://www.sycelectronica.com.ar/)

# Modelado 3D

Estos videos aportan información al modelado de la caja 3D y manipulación suficiente de los modelos 3D para satisfacer las necesidades del trabajo. No son obligatorios, escoja los que necesite.

En caso de tener que hacer la bornera en 3D estas son las especificaciones. (https://drive.google.com/file/d/18XgzW9ulXPOdD6E22yCFbQxx7nZUMB8h/view)

En caso de hacer los modelos en OpenSCAD y querer pasarlos a FreeCAD este es un tutorial. (https://drive.google.com/file/d/1S1sycL9QwSyFjPzkqDW3M9X2tt18jaiq/view)

## Exportación PCB y modelado e impresión 3D

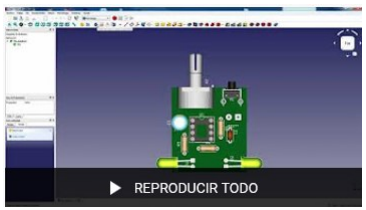
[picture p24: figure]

Serie de videos que explican de manera simple como hacer la caja en FreeCAD a partir del modelo 3D hecho en KiCAD. Estas explicaciones son esenciales.

## Truco para hacer caja


Este método simplifica bastante el proceso de hacer una caja. Muy recomendado.

## Texto sobre cuerpos

Esta es una explicación dedicada de la materia para poner texto sobre el cuerpo para realizar relieve y bajorrelieve. Tiene ciertos inconvenientes: cuando se representa el cuerpo a una hoja el texto no tiene una presentación agradable. Está basado en el video de arriba.


## Cotas completas FreeCAD


En el video se explica cómo acotar las diferentes vistas de un cuerpo y como completar el rótulo.

## Cables en el modelo 3D [opcional]


Dada la demanda de tiempo que lleva realizarlo no les exigimos que el modelo 3D tenga cables hasta la bornera, pero si lo desea hacer puede utilizar este método.

# Impresión 3D

Estos últimos 2 videos están dedicados al perfeccionamiento de la textura de las impresiones 3D. No son necesarias, dado que elevan el presupuesto. Como se menciona en la sección de impresión 3D del informe, una alternativa es la lija, que lo deja liso, pero si no se hace con cuidado deja manchones. Para información sobre impresión 3D puede ver este apunte del Labi. (http://labi.fi.uba.ar/sites/default/files/LABi%20Curso%20-%20Intro%20al%20Modelado%20e%20Impresion%203D.pdf)

PLA: ácido poliláctico

ABS: acrilonitrilo butadieno estireno.

## Acabado liso con ABS [opcional]

El material ABS ante la acetona tiene una “desintegración”, lo que le da un aspecto pulido, pero le da más detalle.


## Acabado liso con PLA [opcional]


Así como el ABS tiene a la acetona, para el PLA está el cloroformo, en este video se usa una alternativa para evitar usarlo tanto por sus efectos biológicos como por su pérdida de calidad.

# Condiciones del trabajo práctico

# Informe

## Estética del informe

Pedimos que los ítems, subitems y otras jerarquías estén marcados de manera adecuada. Carátula como la pedida en los pre informes con el nombre del profesor adjunto. Páginas enumeradas, sin incluir la caratula. Simple faz. Hoja A4. Márgenes de 1 cm por lado por lo menos (queda a criterio del estudiante). Nombre del alumno, fecha de la presentación con número de llamado ese cuatrimestre y fecha de regularización (cuatrimestre y año) en el encabezado. Sangrías y tipografía queda a criterio del alumno. El cuerpo del texto debe ser justificado. Puede hacerlo en cualquier editor de texto. Debe enumerar las figuras y ecuaciones, y enunciarlas cuando corresponda. Haga referencias oportunamente de sus fuentes o bibliografía.

Aconsejamos aprovechar este trabajo para iniciarse en Latex. Puede leer este apunte del Labi (http://labi.fi.uba.ar/labi/cursos/latex) o este libro de Springer (https://link.springer.com/book/10.1007%2F978-3-319-47831-9) para informarse. Latex le otorgará buena prolijidad a su trabajo y le servirá para el resto de la carrera.

La impresión puede ser en blanco y negro, aunque hay ilustraciones que son más claras a color. Pedimos que las hojas no estén arrugadas, previamente usadas, con rayones o manchas notables. Puede consultar a los profesores sobre alguna flexibilización.

## Objetivo

Para este punto recuerde que le debe hacer y que aprendió en la materia. No hace falta que
desarrolle mucho. Básicamente deberá poner en práctica las herramientas aprendidas en el curso para facilitar la realización de un circuito y comparar los resultados esperados de la simulación con la efectiva práctica.

## Características generales del circuito

Durante esta parte se describirá al circuito en sí, para no divagar mucho y poner puntos concretos se proponen una serie de puntos que recomendamos abarcarlos en tal orden.

Síntesis: Decir brevemente que es ese circuito. Cuál es su componente principal, usos que tiene el circuito, el resultado anunciado por el profesor. Puede tomar ideas del pre informe para describir esta parte.

Esquemático: Una opción, formal, es incorporar este como una hoja exclusiva con su correspondiente rótulo que, por una cuestión de lectura, sería agradable que sea vertical, ya que el resto del trabajo está en dicha alineación. Si lo hace horizontal no importa, pero recuerde en ambos casos llenar el rótulo. En caso de optar por ponerlo como una figura de tamaño adecuado (cómodo para la lectura) en el contenido del trabajo, también es aceptable. Si quiere puede poner ambas formas, para hacer referencias dentro del trabajo y mantener la formalidad, se considerará muy agradable.

Funcionamiento: Acá se pide un resumen del funcionamiento del circuito, como ya se pidió en el pre informe. De hecho, es muy aconsejable, a partir del pre informe sacar lo esencial para explicar el funcionamiento del mismo. Debe ser un resumen de un párrafo.

Lista de materiales y costo: Si bien puede basarse en lo realizado en los pre informes debe actualizar bastante esta parte. Sugerimos que lo plantee en forma de cuadro: material, modelo/característica y costo. Separe los costos de consumibles y reutilizables, como el ácido (pierde pureza), mechas finas y servicios (impresión, fotocopia, LCI), de los de la placa y la impresión 3D. En caso de tener alguno de los reutilizables previo al trabajo ponga “0”. En caso de tener alguno de los componentes previo al trabajo ponga un “*” al lado del nombre del componente y averigüe el precio cuando compre el resto de los componentes.

PCB: Lo mismo que el esquemático, solo que acá se haría más hincapié en realizar una miniatura del mismo y no una página dado que ocupa muy poca superficie sobre una hoja, pero cualquier opción dicha en la parte de esquemático es válida.

Resultados esperados: Esta parte también se debe sacar del pre informe. A partir de la información que buscaron del circuito, cuál debería ser el resultado.

## Procedimiento

Durante esta parte se explica cómo fueron elaborando cada producto, el paso a paso, inconvenientes técnicos, errores, herramientas que usaron, intentos fallidos, precauciones que hayan tomado y el tiempo. Aclare los recursos que el Labi le haya dado.

Herramientas: Enumere todas las herramientas usadas(puede no enlistar con viñetas). No hace falta que provea sus características, a excepción de que tal influya en el procedimiento.

Producción PCB: Para este producto deben elaborar demasiado y poner todos los detalles de procedimiento indicados arriba con mucha atención. Es muy importante que, en la parte técnica, anote los tiempos que le llevo cada proceso, el tiempo del paso a paso. En la defensa oral es muy probable que le pregunte sobre la elaboración del PCB, por tal motivo debe hacerla detallada y con atención. Esto abarca desde el layout listo hasta que la placa ya está funcionando definitivamente.

Producción modelos 3D y planos: sobre este no aplica tanto lo escrito en procedimiento, quizás solo el paso a paso, sintético, o como encaró el procedimiento para hacerlo y si hubo alguna dificultad. El tema del tiempo acá no es necesario, a lo sumo algo global. Recuerde que parte de esto ya lo hizo en el pre informe. Lea la siguiente parte para saber que debe excluir.

Producción de la caja: Esta parte abarca realizar el modelo 3D de la caja a partir del modelo 3D del PCB, incorporarlo en el simulador 3D, correrlo, mandarlo a imprimir y tenerlo definitivo. Todo lo que suceda en el medio (menos la parte de planos), se incorpora acá. Incluya el tiempo de impresión con su configuración en el Cura, puede ser tabla, imagen o texto. En caso de que tenga impresora 3D es importante el que agregue el tiempo de impresión real y en caso de no tener agregue el tiempo desde que lo mandó a imprimir hasta que lo tuvieron listo. A partir de tenerlo listo, en sus manos, para ambos casos, anote cuanto tiempo después pudo colocar el circuito en el gabinete.

## Resultados

En este espacio ponga los resultados finales, también mencione resultados que resultaron fallidos y necesitaron algún ajuste. Describa tamaño del PCB real final, irregularidades, pistas corregidas con estaño, pads que no toleraron las conexiones. Con el funcionamiento del circuito y la caja describa lo mismo: características principales, imperfecciones y resultado final (acabado, textura, etcétera).

## Conclusiones

Diferencias con el modelo ideal, tanto físico como funcional, comparativa con otros modos de hacer PCB (planchado vs serigrafía vs LCI vs “mandarlo a China”), posibles usos, opiniones ¿Qué cambiaría si tuviera que hacerlo de nuevo en el futuro?

## Se deben incluir las siguientes imágenes

Algunas de las imágenes, como esquemático y PCB de todas las capas ya se han aclarado en otras partes de la explicación como pueden presentarse. El hecho de que está parte del informe este aquí, no quiere decir que deba colocar las imágenes acá. De hecho, debe colocar todas las imágenes en el lugar adecuado del informe. Aquí solo se menciona cuales deben aparecer. De las imágenes de PCB se espera que pueda meter las 3 (o 2) alineadas en una fila, ya que no ocupan más de 4 mm de ancho.

Imágenes de modelo 3D: Pedimos que sean imágenes claras de la placa, la caja y la tapa y la placa dentro del gabinete (una opaco y otra semitransparente). Con una de cada uno alcanza. En caso de haber componentes personalizados deberá colocar 2 imágenes de cada uno de estos.

Para los planos: Para esta parte puede retirar el padrón en relieve. La “caja y tapa” (plano 1) deben tener una vista isométrica, apoyado sobre la base, acotado donde encastra la tapa (2 cotas) y 2 vistas que complementen los datos con acotaciones necesarias. Para “circuito 3D” (plano 2) repita el procedimiento, pero las 2 cotas de vista isométrica que sean de la base y las 2 vistas complementarias que acoten solo aquellas partes que influyen en la caja. Para “caja, tapa y circuito 3D” (plano 3) es necesario una perspectiva explotada, el alumno tiene que adecuar un criterio de espacio para acomodar y acotar los elementos. Componentes personalizados (plano 4 en adelante) son los planos de aquellos componentes que se pidieron realizar de manera personalizada en 3D. Al igual que con el esquemático y el PCB, se aceptan tanto en hoja a parte con rótulo como miniaturizado en figuras (dibujos de un mismo plano aconsejamos ponerlos en fila). La diferencia es que acá aceptamos hoja entera o figura, de cada plano. Permitimos que, los “plano 1” y “plano 2”, si entran de manera adecuada, los pongan en la misma hoja con rótulo. En cuanto al “plano 3” si se usa una figura se aconseja utilizar casi toda la hoja para que sea bien claro.

No importa que las imágenes no sean a color, pero sí que sean claras.

# Características del circuito (PCB)

Acá puede ver el modelo de la bornera. (https://drive.google.com/file/d/18XgzW9ulXPOdD6E22yCFbQxx7nZUMB8h/view)

La descripción de lo pedido en las consignas del trabajo práctico en este punto es precisa. Por dudas técnicas consulte esta guía más arriba. Si no, no dude en consultar a los profesores.

# Características del gabinete

## Impreso en 3D

La impresión en 3D tiene que ser de plástico. Lo más común es ABS o PLA. Recuerde que el Labi tiene un servicio de impresión 3D. (http://labi.fi.uba.ar/impresiones) Puede acudir a tal con un descuento por ser trabajo práctico para una materia. Le pasaremos una lista al Labi de los regularizados para accedan al descuento, sino puede llevar un papel (http://labi.fi.uba.ar/sites/default/files/labi/impresiones/autorizacion.pdf) firmado para acceder al descuento o enviar una foto de la materia regularizada por mail. Para estimar un presupuesto (http://labi.fi.uba.ar/impresiones/precio) a partir del tiempo impresión en Cura. Si la impresión 3D es un tema de su agrado le avisamos que el Labi organiza reuniones sobre modelado e impresión 3D.

## Lo más pequeño posible

La placa debe tener una holgura mínima, es indispensable que los componentes eviten sufrir daños ante oscilaciones. Recuerde hacer la superficie interior de la caja unas décimas de milímetros más grande que el PCB. Una prueba sencilla para corroborar que cumple es no escuchar ruidos al agitar la caja con el PCB ni sentir golpecitos al hacerlo.

## Debe tener una tapa (también impresa)

Es esencial que la caja cierre con el PCB adentro y la tapa puesta. Lo único que puede sobresalir es cualquier componente con su respectivo orificio. Es fuertemente recomendable que la caja encastre con la tapa. Para esto se le hace un bajorrelieve, de 2 mm, sobre la parte interna, del borde de la caja, con 1 mm de espesor, que encastra con la tapa y a la tapa se hace un relieve de 2 mm de altura que encastre en la ranura anteriormente mencionada (sería como un “negativo” de los últimos 2 mm de la caja, donde al juntarse forman un macizo de 2 mm).

## Tiempo de impresión menor a 75 minutos (CURA)

Las configuraciones que recomendamos son las que están por default. La impresora Prusa i3 (es la que usan en el Labi) es la que debe seleccionar. Si usa una particular y quiere asociar los parámetros con la suya anúncielo en el informe. Las únicas configuraciones que le recomendamos tocar en caso de no saber del tema es la altura (la definición), aconsejamos 0,2 mm (varíe hasta 0,6, no le aconsejamos más). La gente del Labi recomienda que el grosor de las paredes de la caja sea de al menos 2 mm. También recomienda que no le retiren el relleno, déjenlo en 20%. El ángulo de voladizo para el soporte, puede cambiarlo si tiene alguna estructura curva que lo amerite, sino déjelo como esta por default. Estas son todas las configuraciones que se explicaron en clase.
Desmontable para que se pueda retirar el PCB.

Es importante que el PCB sea extraíble de la caja sin grandes impedimentos.

## Contenido

Dentro de la caja deben caber, el PCB, como ya se mencionó, con algunas décimas de milímetro de holgura (el interior de la caja debe ser un poco más grande que el PCB) y la pila. Algunos alumnos en otros cuatrimestres han hecho una porta pila como parte de la caja adhiriéndole 2 chapitas (una en cada polo).

## Orificios

La única manera (por consigna) de hacer agujeros a la caja, o la tapa, es mediante la impresión 3D y dichos orificios deben estar en modelo 3D, sin embargo, ante el costo que tiene realizar la impresión es un ítem que se puede flexibilizar. Recomendamos no hacer orificios de más, solo los necesarios (si sabe del tema haga estructura que desee mientras cumpla las consignas). A la hora de hacer el modelo 3D haga los orificios un 10% a 20% (a ojo) más grandes de lo que le exige el componente. En caso de olvidarse agujeros, imperfecciones o errores en tamaño puede acudir a arreglarlo suavemente con algunas herramientas de lijado. No recomendamos usar tornos ya que estos giran muy rápido y por la fricción antes de pulverizar al material, lo derriten. Estoy último también aplica para darle un acabado más liso al material: una vez impreso notaran que las fibras del material son destacables, esto con mucha paciencia y una serie de lijas se puede arreglar (quedará una superficie pulida, pero sensible a rayones y muy posiblemente quede manchada) para que quede con una textura agradable al tacto.

# Sugerencias, opiniones y contacto

La relevancia de este documento se hace entre todos. Quisiéramos saber tu opinión o critica respecto a este documento. Si falta algo, si se entendió, si te sirvió, si hay algo confuso o si simplemente fue de tu agrado.

Recomendamos llenar este formulario una vez leído todo el apunte.

Te invitamos a que rellenes este formulario. (https://forms.gle/Styc97Y2ZMSSUVsW7)

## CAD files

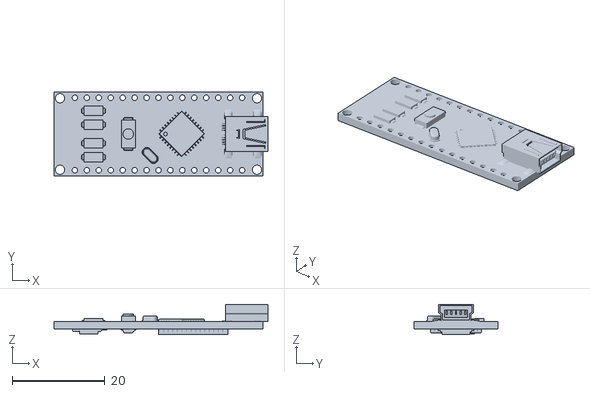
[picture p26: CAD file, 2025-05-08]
modulo_seguidor/models/Arduino Nano.stl
46.1 x 18.0 x 6.55

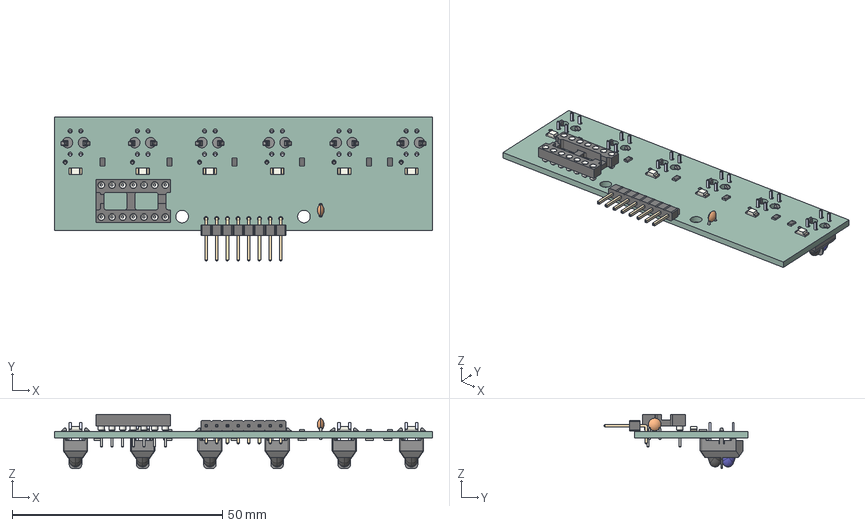
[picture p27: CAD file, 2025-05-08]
modulo_sensor/exports/modulo_sensor.step
90.0 x 34.2 x 12.9 mm
PinHeader_1x08_P254mm_Horizontal
R_0805_2012Metric x 18
LED_1206_3216Metric x 6
DIP_14_W762mm_Socket
C_Disc_D30mm_W16mm_P250mm
TCRT5000 x 6
modulo_sensor_PCB

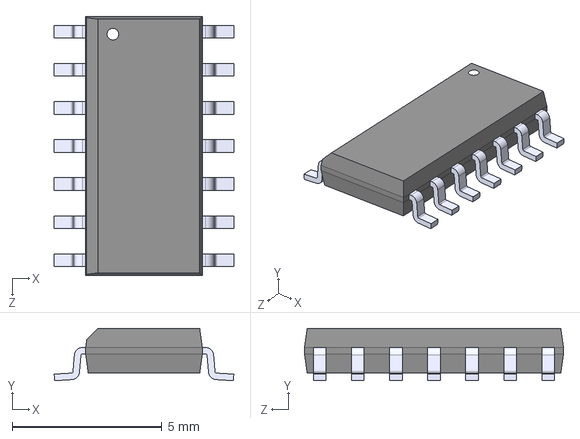
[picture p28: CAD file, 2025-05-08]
modulo_sensor/step/74HC14DR2G.step
6.00 x 1.75 x 8.65 mm

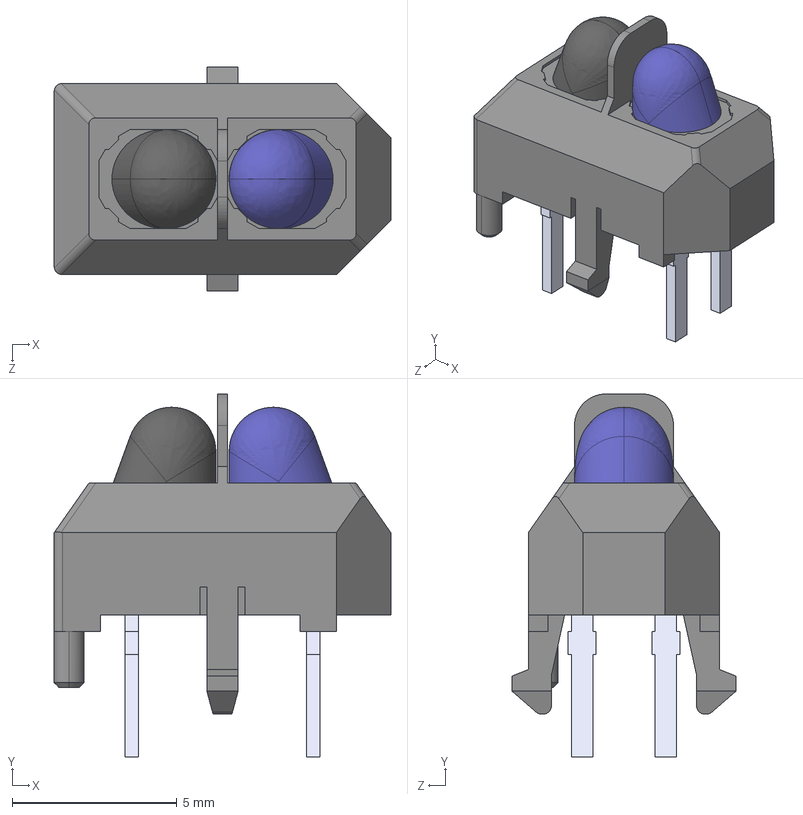
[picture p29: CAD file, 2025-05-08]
modulo_sensor/step/TCRT5000.step
10.2 x 11.0 x 6.80 mm

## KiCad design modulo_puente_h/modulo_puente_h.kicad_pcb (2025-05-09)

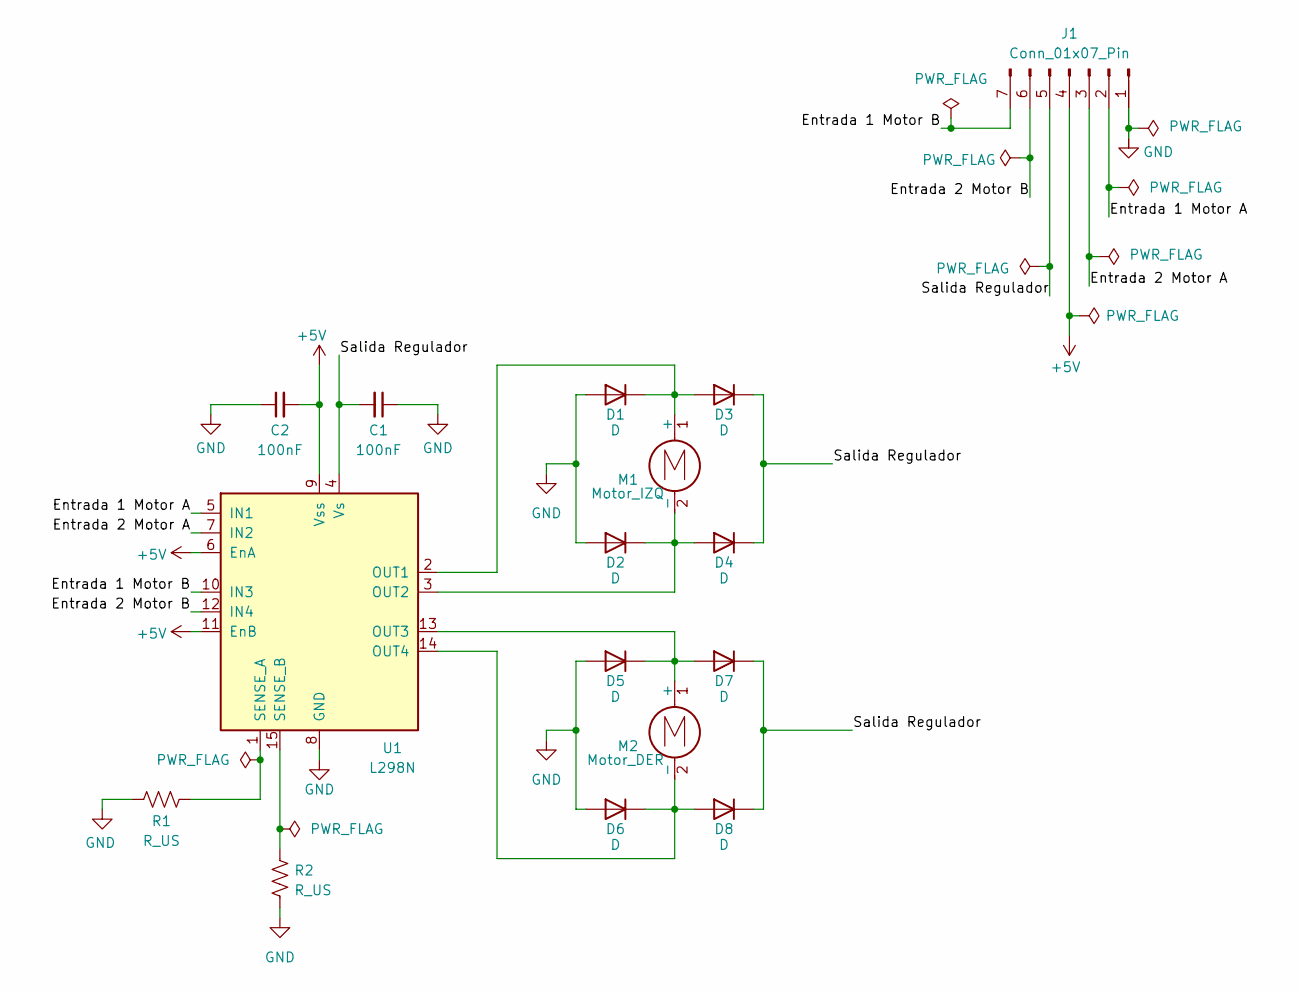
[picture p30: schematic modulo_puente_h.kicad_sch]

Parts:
C1, C2: 100nF; C_Disc_D7.0mm_W2.5mm_P5.00mm
D1, D2, D3, D4, D5, D6, D7, D8: D; D_DO-41_SOD81_P7.62mm_Horizontal
J1: Conn_01x07_Pin; PinHeader_1x07_P2.54mm_Vertical
M1: Motor_IZQ; R_Axial_DIN0207_L6.3mm_D2.5mm_P2.54mm_Vertical
M2: Motor_DER; R_Axial_DIN0207_L6.3mm_D2.5mm_P2.54mm_Vertical
R1, R2: R_US; R_0805_2012Metric_Pad1.20x1.40mm_HandSolder
U1: L298N; TO-220-15_P2.54x2.54mm_StaggerOdd_Lead4.58mm_Vertical

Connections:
+5V: C2.2, J1.4, U1.6 (EnA), U1.9 (Vss), U1.11 (EnB)
/Entrada 1 Motor A: J1.2, U1.5 (IN1)
/Entrada 1 Motor B: J1.7, U1.10 (IN3)
/Entrada 2 Motor A: J1.3, U1.7 (IN2)
/Entrada 2 Motor B: J1.6, U1.12 (IN4)
/Salida Regulador: C1.2, D3.1 (K), D4.1 (K), D7.1 (K), D8.1 (K), J1.5, U1.4 (Vs)
GND: C1.1, C2.1, D1.2 (A), D2.2 (A), D5.2 (A), D6.2 (A), J1.1, R1.2, R2.1, U1.8 (GND)
unnamed: D1.1 (K), D3.2 (A), M1.1 (+), U1.2 (OUT1)
unnamed: D2.1 (K), D4.2 (A), M1.2 (-), U1.3 (OUT2)
unnamed: D5.1 (K), D7.2 (A), M2.1 (+), U1.13 (OUT3)
unnamed: D6.1 (K), D8.2 (A), M2.2 (-), U1.14 (OUT4)
unnamed: R1.1, U1.1 (SENSE_A)
unnamed: R2.2, U1.15 (SENSE_B)

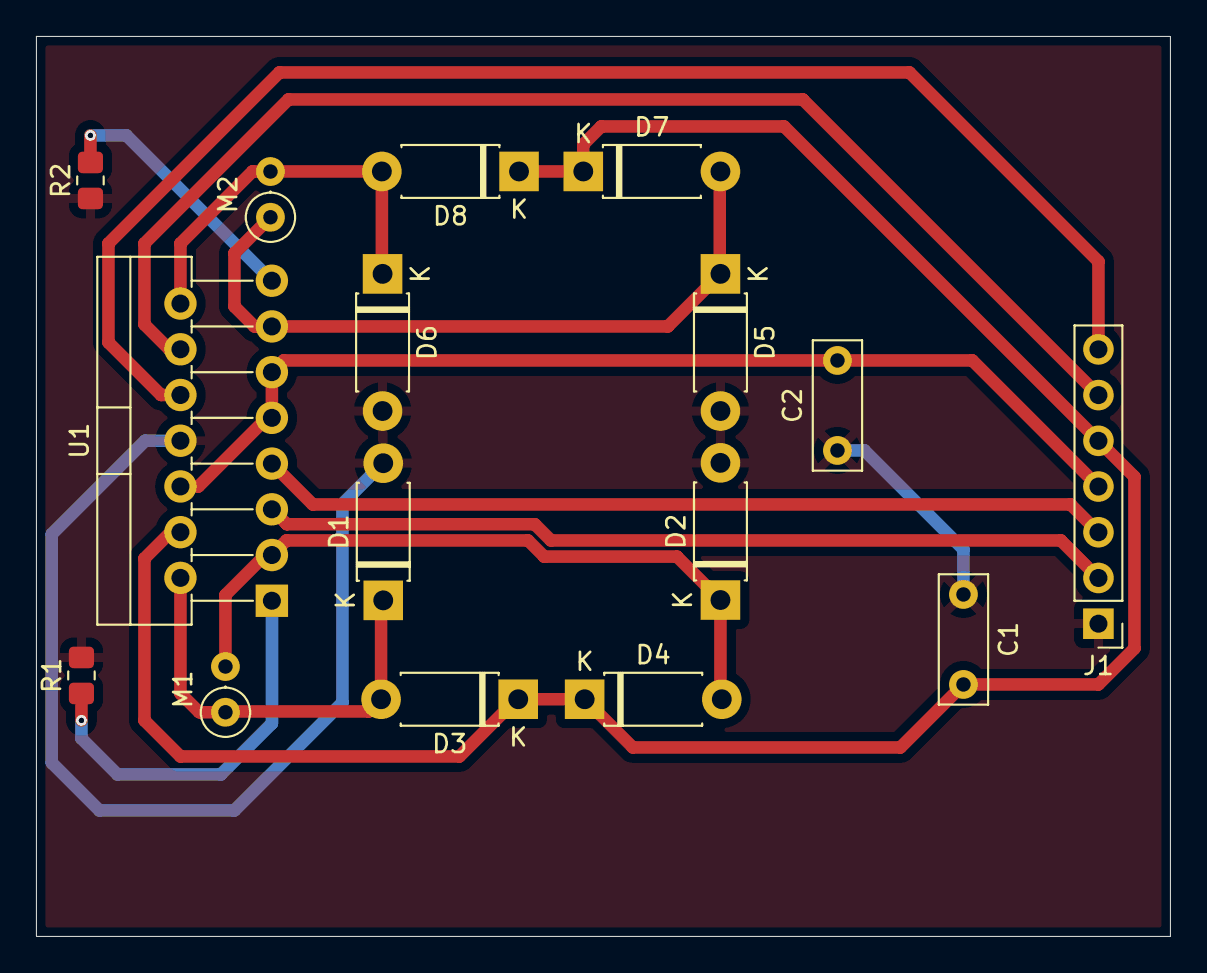
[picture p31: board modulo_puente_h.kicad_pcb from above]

Board: 2 copper layers, 63.0 x 50.0 mm, 16 parts (0 on the bottom side), 13 nets.

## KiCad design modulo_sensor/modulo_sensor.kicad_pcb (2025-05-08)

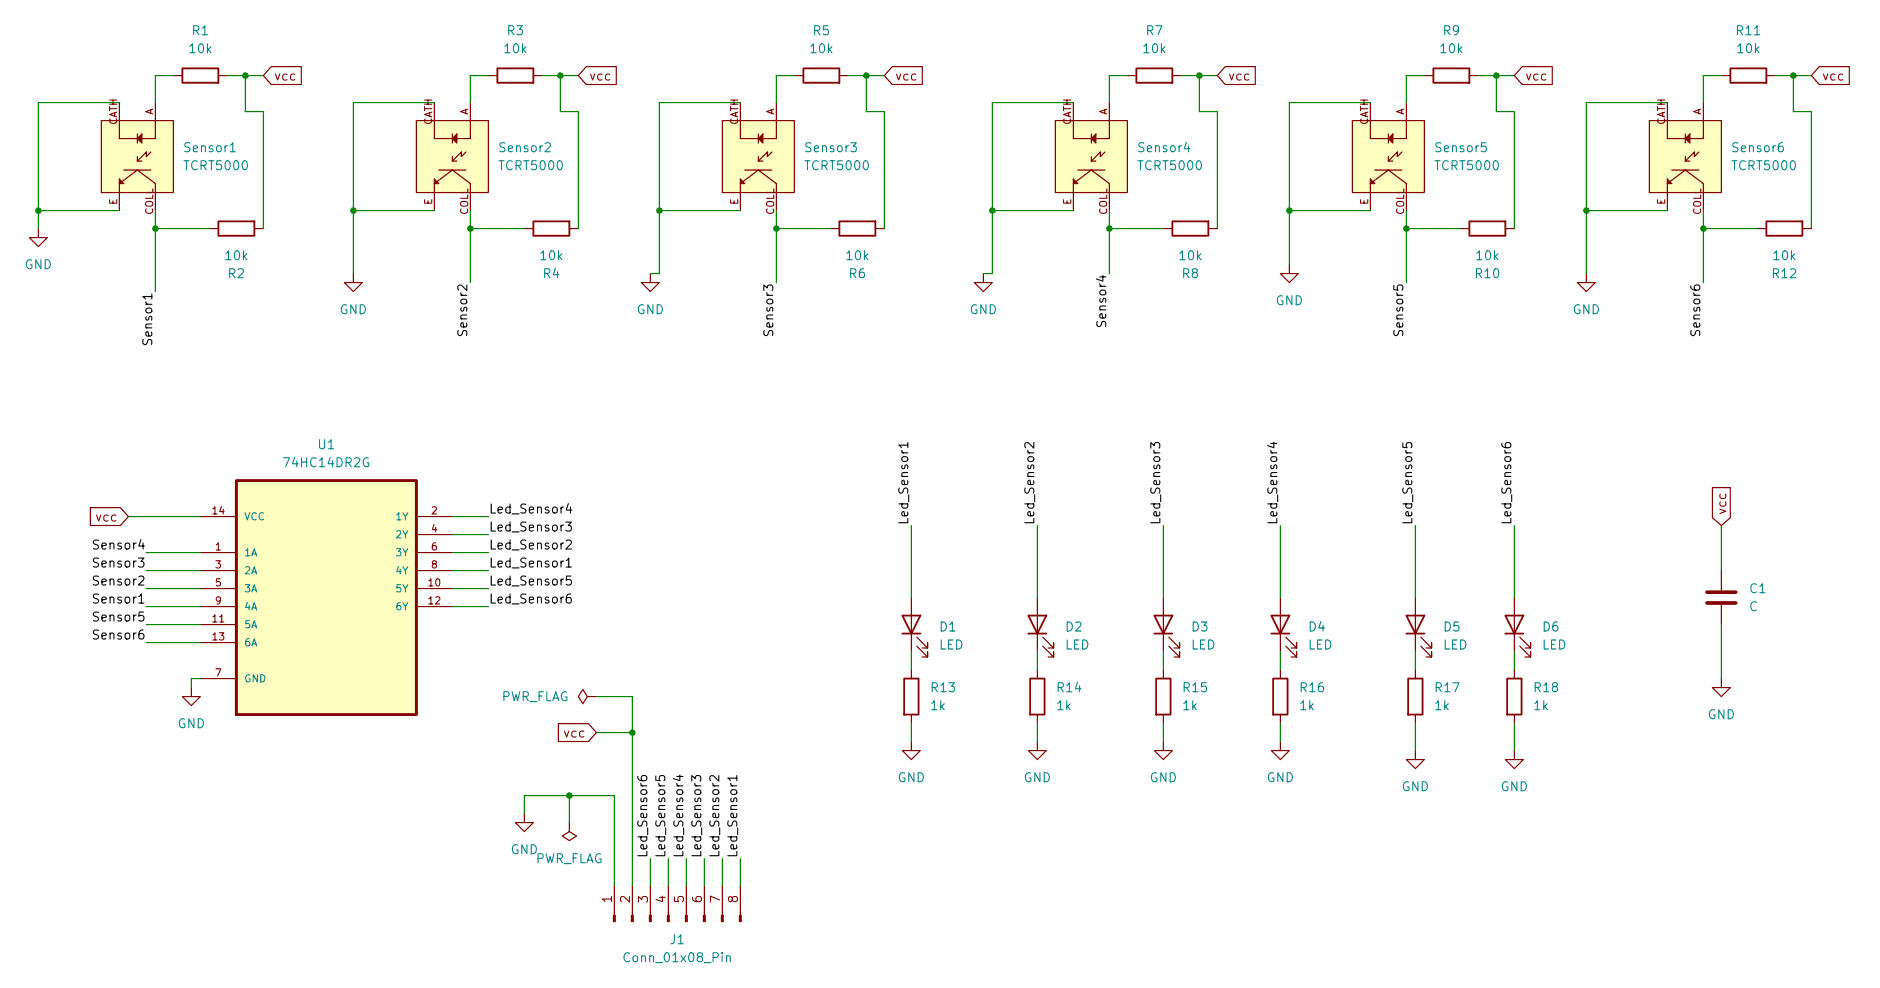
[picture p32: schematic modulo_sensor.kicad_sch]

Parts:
C1: C; C_Disc_D3.0mm_W1.6mm_P2.50mm
D1, D2, D3, D4, D5, D6: LED; LED_1206_3216Metric_Pad1.42x1.75mm_HandSolder
J1: Conn_01x08_Pin; PinHeader_1x08_P2.54mm_Horizontal
R1, R2, R3, R4, R5, R6, R7, R8, R9, R10, R11, R12: 10k; R_0805_2012Metric_Pad1.20x1.40mm_HandSolder
R13, R14, R15, R16, R17, R18: 1k; R_0805_2012Metric_Pad1.20x1.40mm_HandSolder
Sensor1, Sensor2, Sensor3, Sensor4, Sensor5, Sensor6: TCRT5000; OPTO_TCRT5000; PARTREV 1.7
U1: 74HC14DR2G; DIP-14_W7.62mm_Socket; MPN 74HC14DR2G

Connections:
/Led_Sensor1: D1.2 (A), J1.8, U1.8 (4Y)
/Led_Sensor2: D2.2 (A), J1.7, U1.6 (3Y)
/Led_Sensor3: D3.2 (A), J1.6, U1.4 (2Y)
/Led_Sensor4: D4.2 (A), J1.5, U1.2 (1Y)
/Led_Sensor5: D5.2 (A), J1.4, U1.10 (5Y)
/Led_Sensor6: D6.2 (A), J1.3, U1.12 (6Y)
/Sensor1: R2.1, Sensor1.COLL, U1.9 (4A)
/Sensor2: R4.1, Sensor2.COLL, U1.5 (3A)
/Sensor3: R6.1, Sensor3.COLL, U1.3 (2A)
/Sensor4: R8.1, Sensor4.COLL, U1.1 (1A)
/Sensor5: R10.1, Sensor5.COLL, U1.11 (5A)
/Sensor6: R12.1, Sensor6.COLL, U1.13 (6A)
GND: C1.2, J1.1, R13.2, R14.2, R15.2, R16.2, R17.2, R18.2, Sensor1.CATH, Sensor1.E, Sensor2.CATH, Sensor2.E, Sensor3.CATH, Sensor3.E, Sensor4.CATH, Sensor4.E, Sensor5.CATH, Sensor5.E, Sensor6.CATH, Sensor6.E, U1.7 (GND)
unnamed: D1.1 (K), R13.1
unnamed: D2.1 (K), R14.1
unnamed: D3.1 (K), R15.1
unnamed: D4.1 (K), R16.1
unnamed: D5.1 (K), R17.1
unnamed: D6.1 (K), R18.1
unnamed: R1.1, Sensor1.A
unnamed: R3.1, Sensor2.A
unnamed: R5.1, Sensor3.A
unnamed: R7.1, Sensor4.A
unnamed: R9.1, Sensor5.A
unnamed: R11.1, Sensor6.A
vcc: C1.1, J1.2, R1.2, R2.2, R3.2, R4.2, R5.2, R6.2, R7.2, R8.2, R9.2, R10.2, R11.2, R12.2, U1.14 (VCC)

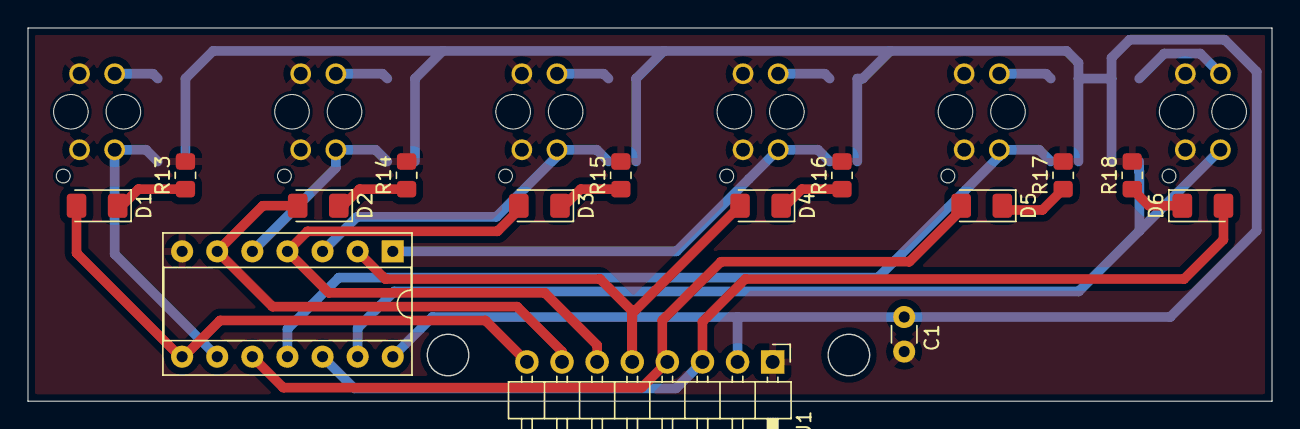
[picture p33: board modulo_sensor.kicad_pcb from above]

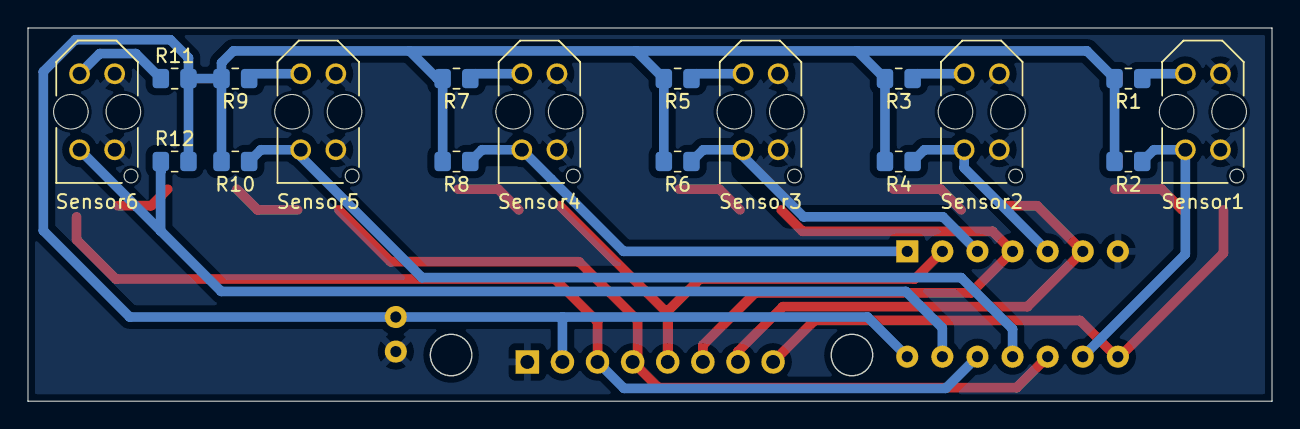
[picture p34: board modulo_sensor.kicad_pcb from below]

Board: 2 copper layers, 90.0 x 27.0 mm, 33 parts (18 on the bottom side), 26 nets.

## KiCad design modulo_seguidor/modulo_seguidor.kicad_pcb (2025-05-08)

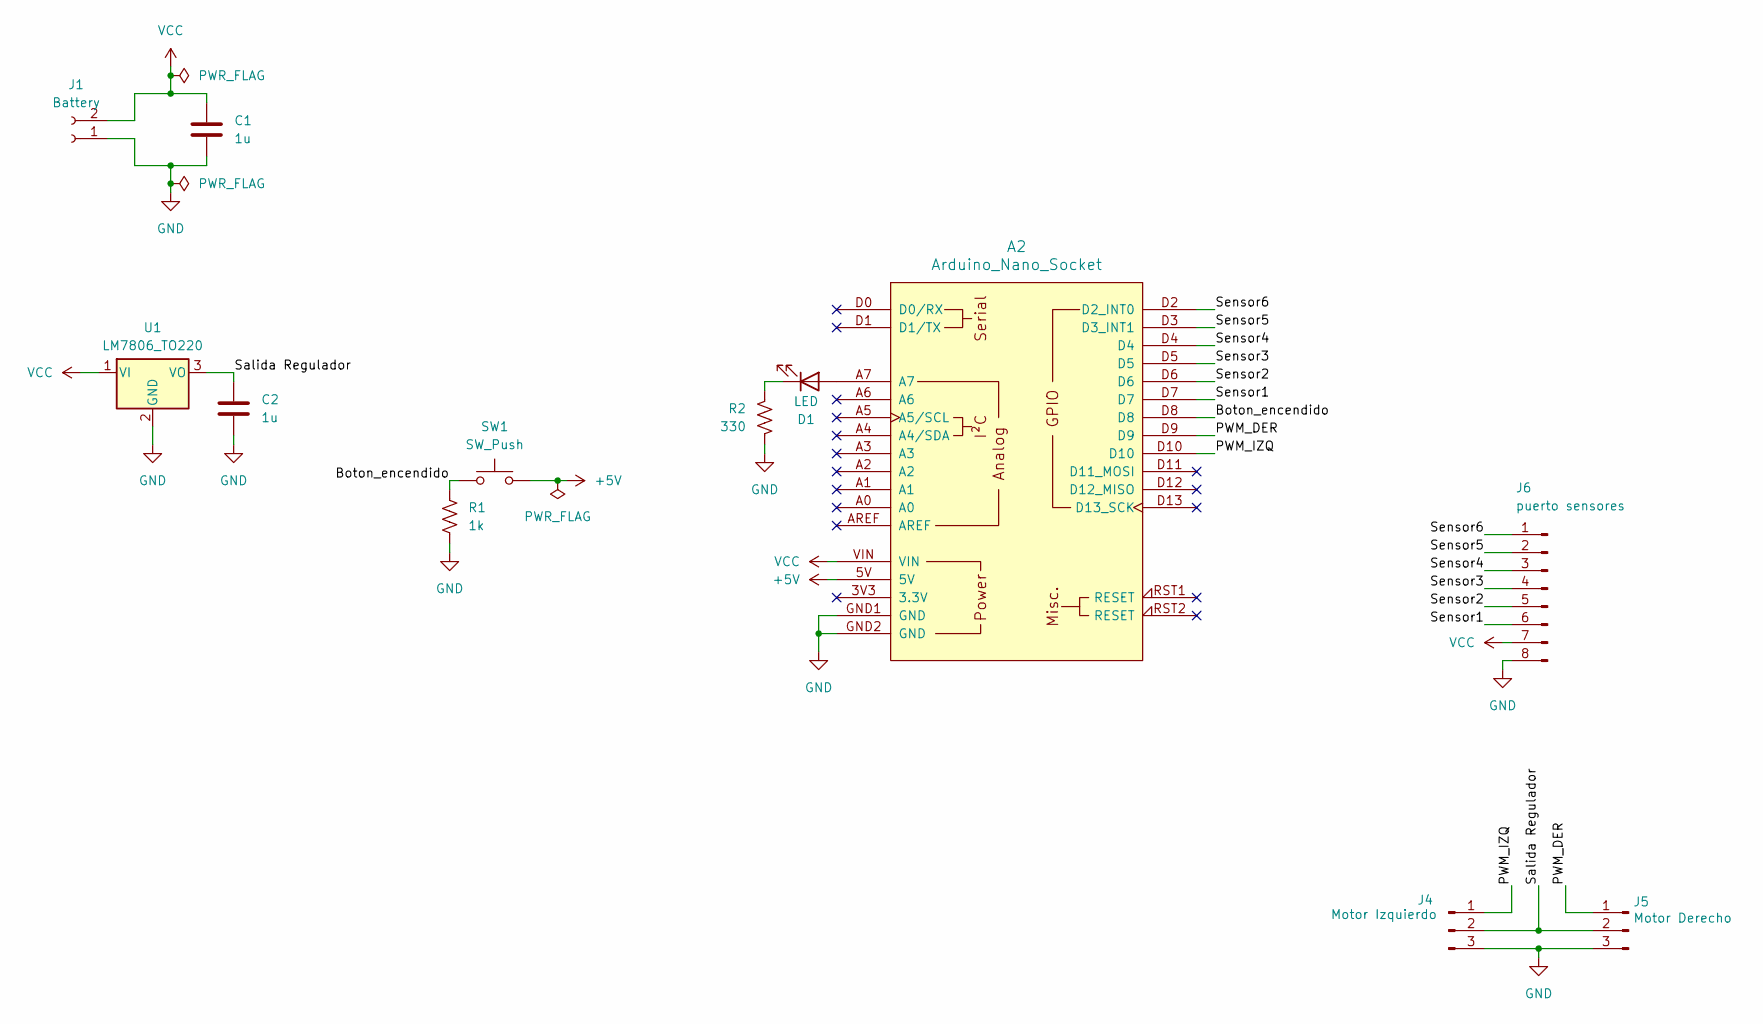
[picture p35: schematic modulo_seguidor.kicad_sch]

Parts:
A2: Arduino_Nano_Socket
C1, C2: 1u; C_Disc_D7.0mm_W2.5mm_P5.00mm
D1: LED; LED_D5.0mm
J1: Battery; Molex_KK-254_AE-6410-02A_1x02_P2.54mm_Vertical
J4: Motor Izquierdo; PinHeader_1x03_P2.54mm_Vertical
J5: Motor Derecho; PinHeader_1x03_P2.54mm_Vertical
J6: puerto sensores; PinHeader_1x08_P2.54mm_Horizontal
R1: 1k; R_Axial_DIN0411_L9.9mm_D3.6mm_P12.70mm_Horizontal
R2: 330; R_Axial_DIN0411_L9.9mm_D3.6mm_P12.70mm_Horizontal
SW1: SW_Push; SW_PUSH_6mm
U1: LM7806_TO220; TO-220-3_Vertical

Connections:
+5V: A2.5V, SW1.1
/Boton_encendido: A2.D8, R1.1, SW1.2
/PWM_DER: A2.D9, J5.1
/PWM_IZQ: A2.D10, J4.1
/Salida Regulador: C2.1, J4.2, J5.2, U1.3 (VO)
/Sensor1: A2.D7, J6.6
/Sensor2: A2.D6, J6.5
/Sensor3: A2.D5, J6.4
/Sensor4: A2.D4, J6.3
/Sensor5: A2.D3 (D3_INT1), J6.2
/Sensor6: A2.D2 (D2_INT0), J6.1
GND: A2.GND1 (GND), A2.GND2 (GND), C1.2, C2.2, J1.1, J4.3, J5.3, J6.8, R1.2, R2.2, U1.2 (GND)
unnamed: A2.A7, D1.2 (A)
unnamed: D1.1 (K), R2.1
VCC: A2.VIN, C1.1, J1.2, J6.7, U1.1 (VI)

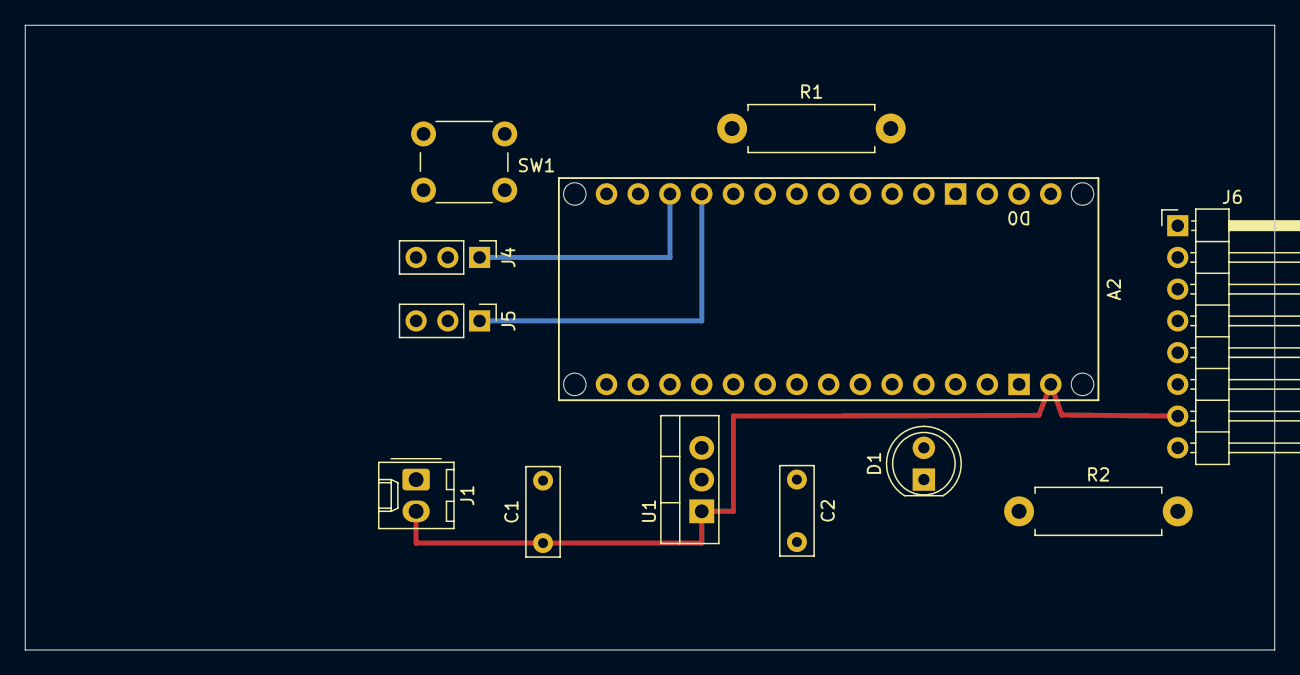
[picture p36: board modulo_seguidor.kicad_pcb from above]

Board: 12 copper layers, 100.0 x 50.0 mm, 12 parts (0 on the bottom side), 15 nets.

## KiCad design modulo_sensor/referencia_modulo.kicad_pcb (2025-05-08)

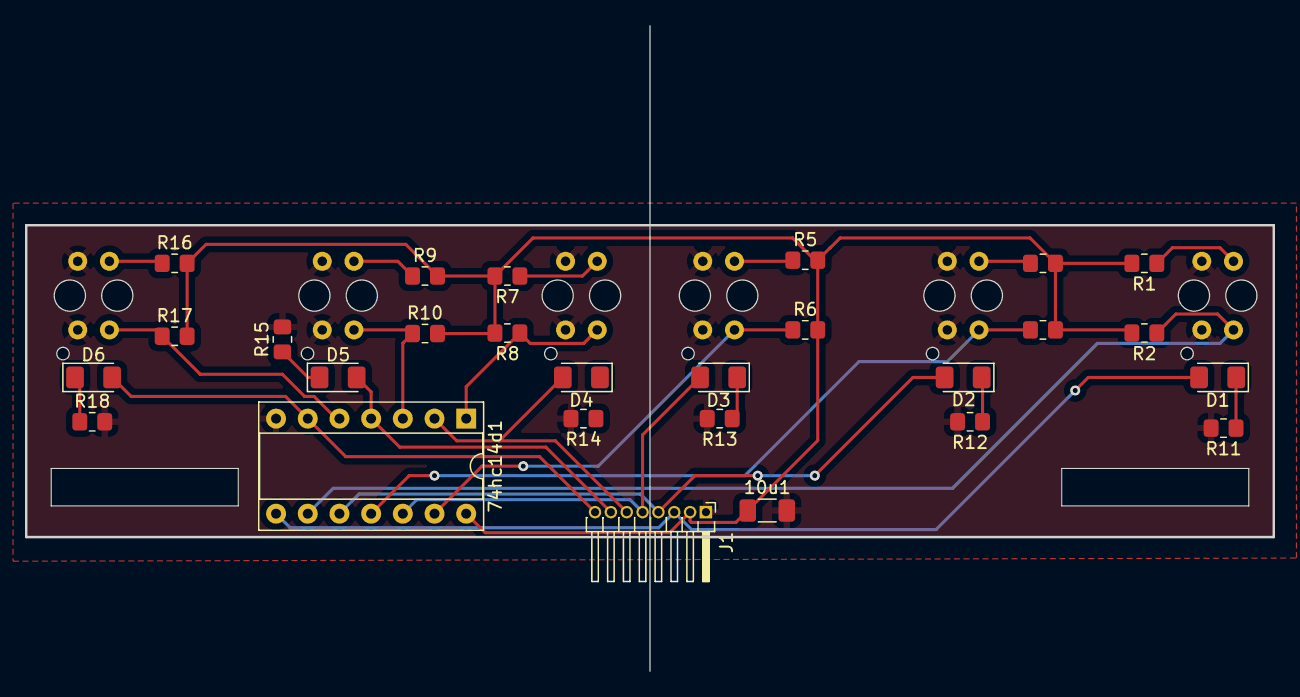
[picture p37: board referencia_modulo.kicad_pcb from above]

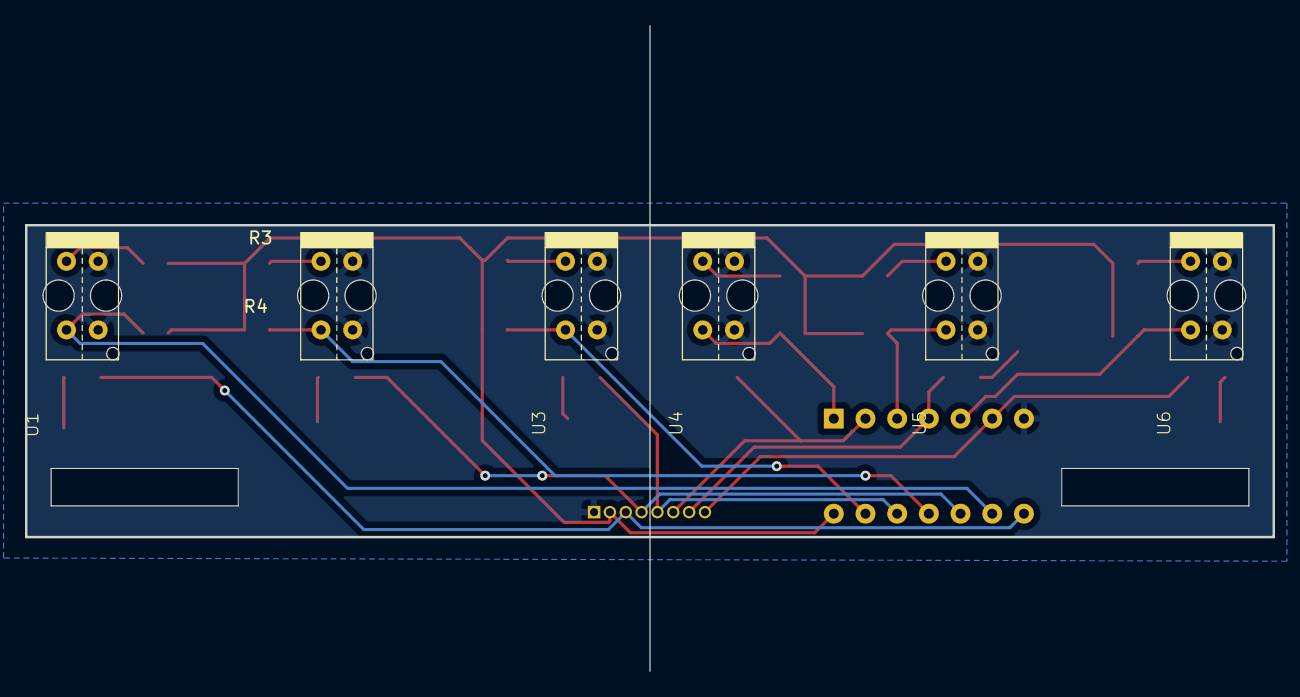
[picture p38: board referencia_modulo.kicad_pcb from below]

Board: 2 copper layers, 100.0 x 25.0 mm, 33 parts (6 on the bottom side), 26 nets.

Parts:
10u1: CAP; C_1206_3216Metric_Pad1.33x1.80mm_HandSolder
74hc14d1: A_14-LC-TT; DIP-14_W7.62mm_Socket
D1, D2, D3, D4, D5, D6: LED; LED_1206_3216Metric_Pad1.42x1.75mm_HandSolder
J1: Conn_01x08_Pin; PinHeader_1x08_P1.27mm_Horizontal
R1, R3, R5, R7, R9, R16: 220; R_0805_2012Metric_Pad1.20x1.40mm_HandSolder
R2, R4, R6, R8, R10, R17: 10k; R_0805_2012Metric_Pad1.20x1.40mm_HandSolder
R11, R12, R13, R14, R15, R18: 1k; R_0805_2012Metric_Pad1.20x1.40mm_HandSolder
U1, U2, U3, U4, U5, U6: TCMT4106; tcrt5000

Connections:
/sensor1: 74hc14d1.8, D1.2 (A), J1.3
/sensor1_unfiltered: 74hc14d1.9, R2.1, U1.16
/sensor2: 74hc14d1.10, D2.2 (A), J1.4
/sensor2_unfiltered: 74hc14d1.11, R4.1, U2.16
/sensor3: 74hc14d1.12, D3.2 (A), J1.5
/sensor3_unfiltered: 74hc14d1.13, R6.1, U3.16
/sensor4: 74hc14d1.2, D4.2 (A), J1.6
/sensor4_unfiltered: 74hc14d1.1, R8.1, U4.16
/sensor5: 74hc14d1.4, D5.2 (A), J1.7
/sensor5_unfiltered: 74hc14d1.3, R10.1, U5.16
/sensor6: 74hc14d1.6, D6.2 (A), J1.8
/sensor6_unfiltered: 74hc14d1.5, R17.1, U6.16
GND: 10u1.2, 74hc14d1.7, J1.1, R11.2, R12.2, R13.2, R14.2, R15.2, R18.2, U1.2, U1.15, U2.2, U2.15, U3.2, U3.15, U4.2, U4.15, U5.2, U5.15, U6.2, U6.15
unnamed: D1.1 (K), R11.1
unnamed: D2.1 (K), R12.1
unnamed: D3.1 (K), R13.1
unnamed: D4.1 (K), R14.1
unnamed: D5.1 (K), R15.1
unnamed: D6.1 (K), R18.1
unnamed: R1.1, U1.1
unnamed: R3.1, U2.1
unnamed: R5.1, U3.1
unnamed: R7.1, U4.1
unnamed: R9.1, U5.1
unnamed: R16.1, U6.1
VCC: 10u1.1, 74hc14d1.14, J1.2, R1.2, R2.2, R3.2, R4.2, R5.2, R6.2, R7.2, R8.2, R9.2, R10.2, R16.2, R17.2

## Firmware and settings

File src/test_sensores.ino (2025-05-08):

/*
  * Disposición de los sensores en el modulo Sensor
  *  _________________________________________
  * |                                         |
  * |    S1    S2    S3    S4    S5    S6     |
  * |    _________                            |
  * |   |Integrado|                           |
  * |_________________________________________|
  *              | | | | | | | |
  *              1 2 3 4 5 6 V GND
  */

#define SENSORS_SIZE 6

typedef enum {
  SENSOR_1 = 2,
  SENSOR_2,
  SENSOR_3,
  SENSOR_4,
  SENSOR_5,
  SENSOR_6,
} SENSOR_PIN_T;


// Estructura representando el estado de los 6 Sensores
struct PinsState {
  bool states[6];

  PinsState(bool must_read) : states{0} {
    if (must_read) this->read();
  }

  // Actualiza el estado de los sensores leyendo de los pines
  void read() {
      for (int i = 0; i < SENSORS_SIZE; i++)
        this->states[i] = digitalRead(SENSOR_1 + i);
  }

  void print() {
    Serial.println("Sensor1\tSensor2\tSensor3\tSensor4\tSensor5\tSensor6");
    for (int i = 0; i < SENSORS_SIZE; i++) {
       Serial.print(states[i]);
       Serial.print("\t");
    }
    Serial.println("\n");
  }

  bool operator==(const PinsState& other) {
    for (int i = 0; i < SENSORS_SIZE; i++)
      if (this->states[i] != other.states[i])
        return false;
    return true;
  }

  bool operator!=(const PinsState& other) {
    return not ((*this) == other);
  }
  
  PinsState& operator=(const PinsState& other) {
	for (int i = 0; i < SENSORS_SIZE; i++)
      this->states[i] = other.states[i];
  }
};


void setup(){
  Serial.begin(9600);
  for (int i = 0; i < SENSORS_SIZE; i++)
       pinMode(SENSOR_1 + i, INPUT);
}

PinsState previous_state(false);

void loop() {
  PinsState current_state(true);
  if (not (current_state == previous_state)) {
    previous_state = current_state;
    previous_state.print();
  }
  delay(100); // Reducir el delay para más precisión
}

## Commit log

2025-05-08 test commit
    [74HC14DR2G.step, Arduino Nano.stl, TCRT5000.step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]
2025-05-09 Deploying to main from @ leithcoX/test-seguidor@514b852d081cf7de3d81e669fe0f0a6481729ef0 🚀
    [74HC14DR2G.step, Arduino Nano.stl, TCRT5000.step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]
2025-05-09 Revert "Deploying to main from @ leithcoX/test-seguidor@514b852d081cf7de3d81e669fe0f0a6481729ef0 🚀"
    This reverts commit 73fc4e96f61ec003882416f7a758038d56a8601e.
    [74HC14DR2G.step, Arduino Nano.stl, TCRT5000.step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]
